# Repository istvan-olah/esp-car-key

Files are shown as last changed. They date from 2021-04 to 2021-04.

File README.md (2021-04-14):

## Automatic car unlock when nearby

 The main issue which this application solves is human forgetfulness, specifically if the car door 
 was locked or not. From my own experience, happens around 40% of the time, that I do not remember it.

 Basic idea is to have a BLE device (a phone, or a smartwatch/fitbit) and when that device is near the car,
the door will open, when it is not in range anymore, the doors will lock automatically.

## How it works?

 The application is configured to search for a specific MAC Address, since they are unique it is considered
secure but there also can be other security features introduced, for example that the device has to be paired
or by implementing a handshake. 

 The configuration part should be done over bluetooth, with a BL serial connection. With this feature, we
don't have to worry about changing our watch/phone, because the app only has to be reconfigured, 
 not reprogrammed.

## Pre-requisites

  - ESP 32-WROOM
  - A relay with 2 separate circuits
  - A remote car key motherboard
  - A BLE device (Android phone/Smartwatch/Fitbit)
  - 3 LED-s with 220 Ohm resistors
  - A 2-way switch
  - A buzzer
  - A DC-to-DC 5v-3.3v converter

## Schematics

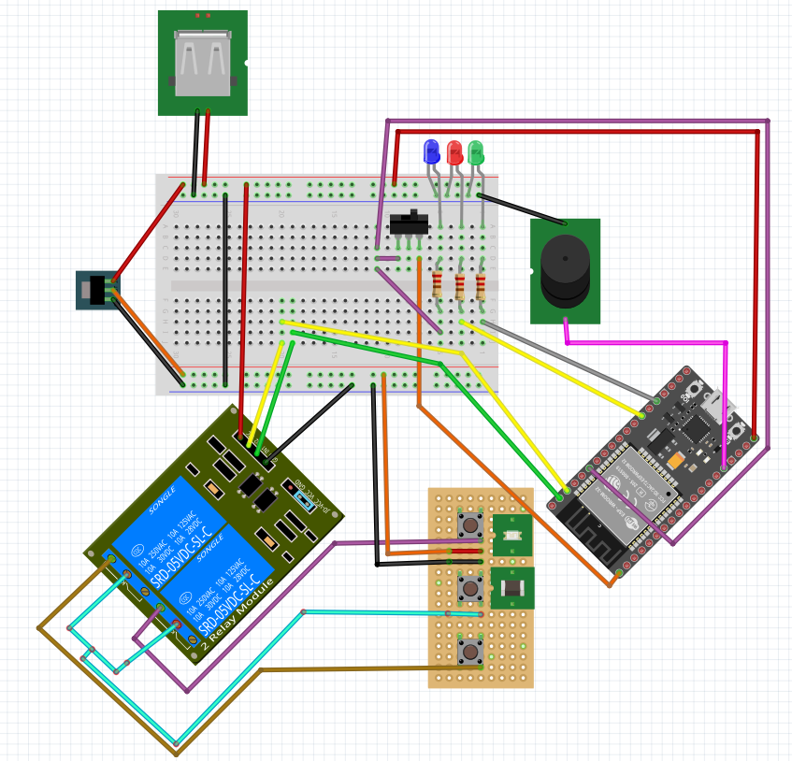
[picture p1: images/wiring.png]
Schematics


### Why use relays?

If we look closely, we can see that we have 2 circuits here. The one which contains the ESP-32
and the one which contains the key motherboard. For safety purposes I made it like this, so we won't
burn the key component, which is the most expensive part of the project and also the one which we have no
schematics or information about it whatsoever. 

## Wiring

### Power connections
 - 5v - ESP IN
 - GND - ESP GND
 - 5v - DC-DC converter input
 - GND - DC-DC converter GND
 - DC-DC output - Key input (where normally the battery goes)
 - GND - Key GND (where normally the battery goes)

### ESP Connections:
 - GPIO 13 - Buzzer
 - GPIO 2 - Green LED (turns on for 1 second when the car is unlocked)
 - GPIO 4 - Red LED (turns on for 1 second when the car is locked)
 - 3.3V - Switch input
 - GPIO 13 - Switch output
 - GPIO 22 - Switch output
 - GPIO 23 - Relay IN-1
 - GPIO 22 - Relay IN-2

 ### Relay connections:
 - COM1 & COM2 - Key common (it can be found with a multimeter, 
   all buttons on the key have that connection in common)
 - NO1 - Key close button's leg 
 - NO2 - Key open button's leg

## 3D Models

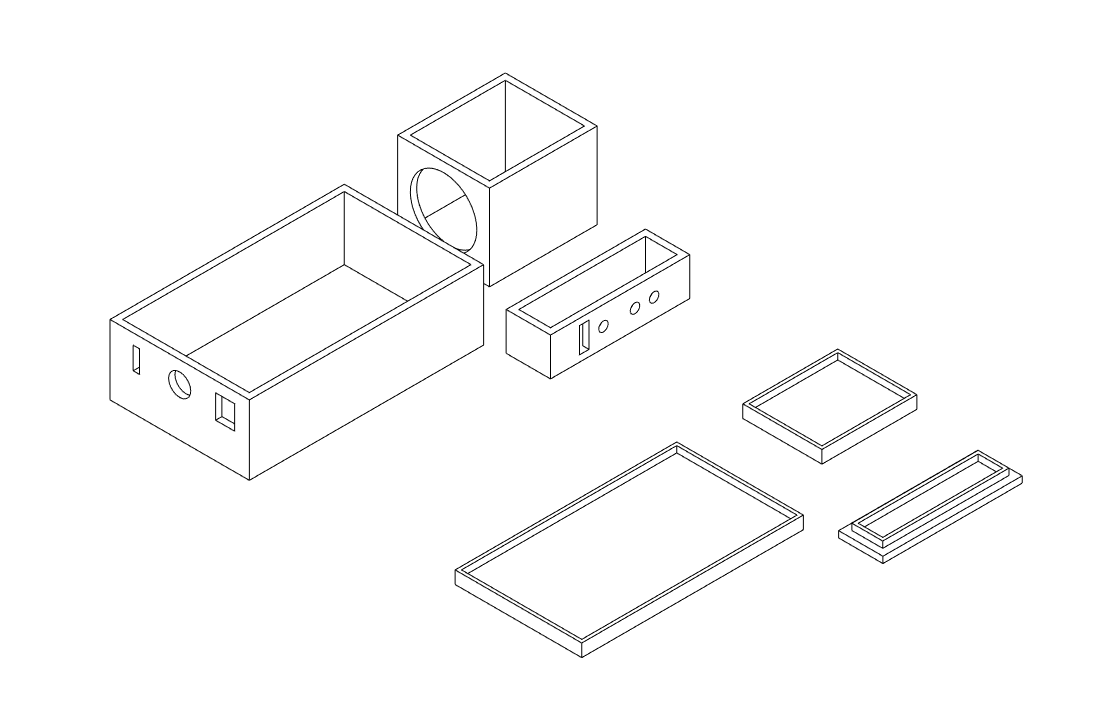
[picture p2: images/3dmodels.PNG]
3D Models


### Final status

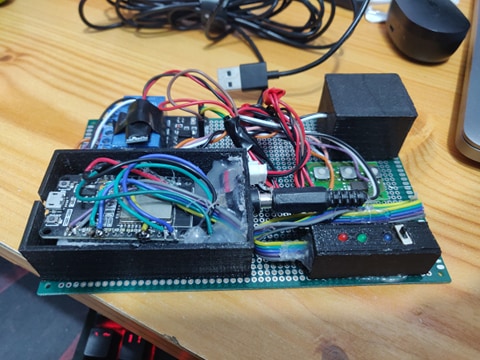
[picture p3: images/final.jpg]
Final


## Set up

 - Write the software onto the hardware using Arduino IDE
 - Download `Serial Bluetooth Terminal` from the [google play store](https://play.google.com/store/apps/details?id=de.kai_morich.serial_bluetooth_terminal&hl=en&gl=US)
 - Turn the switch on the ESP on and pair with the ESP (The name is set through the code)
- Send the following text to the device: 
  `|aa:bb:aa:bb:aa:bb;3500;5200;1100;4750;3;1000|`
     - The first is the mac address of the BLE device which is used as key
     - Second is the open delay (how much to wait after a scan whilst unlocked)
     - Third is the open timeout (how much to wait after the car was unlocked)
     - Fourth is the closed delay (how much to wait after a scan whilst locked)
     - Fifth is the closed timeout (how much to wait after the car was locked)
     - Sixth is the not found in a row (how many scans to wait to close the car if key not found)
     - Seventh is how much time to "press" the buttons on the key (different for each key)

## Putting it in the car 
  Please don't mind the fact that I haven't cleaned the interior in a while

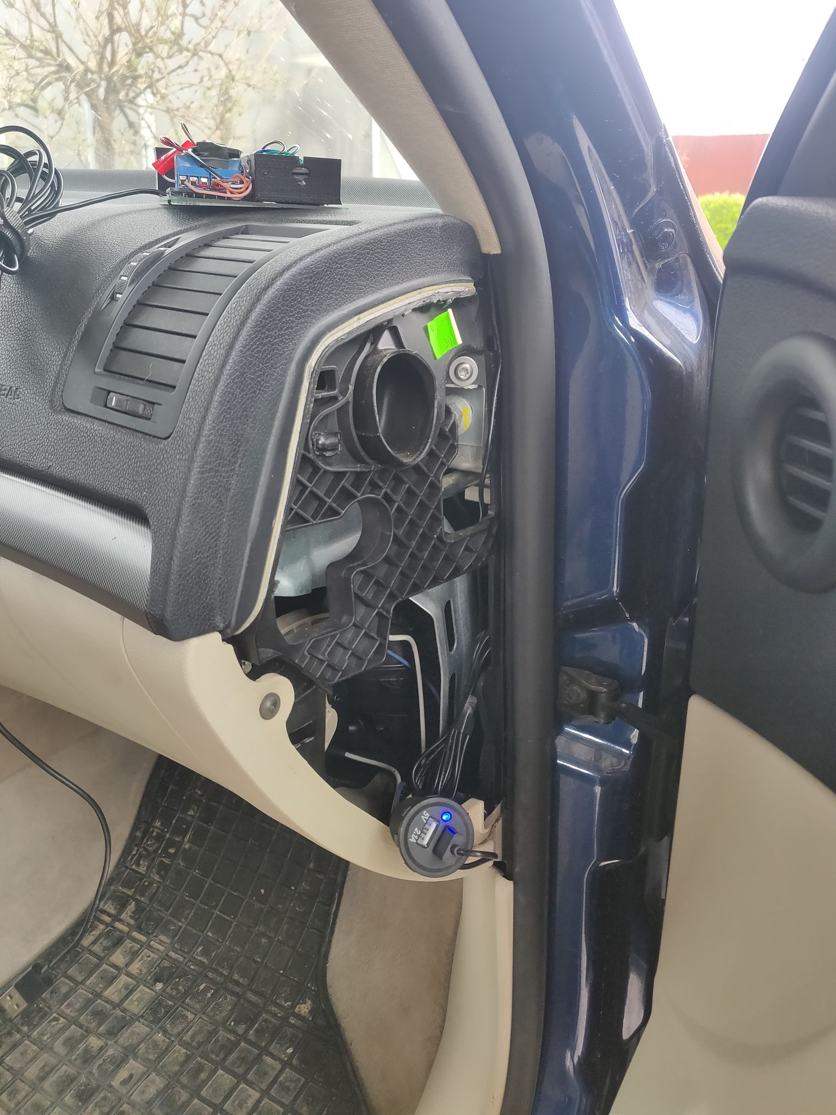
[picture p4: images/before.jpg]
Before
  
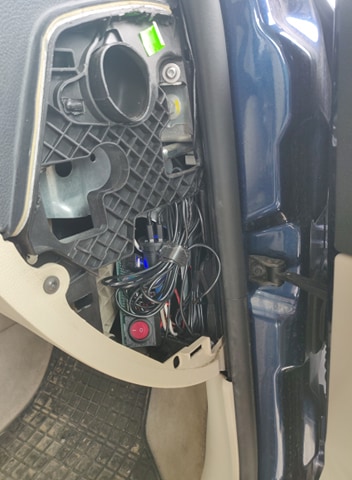
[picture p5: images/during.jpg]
During
  
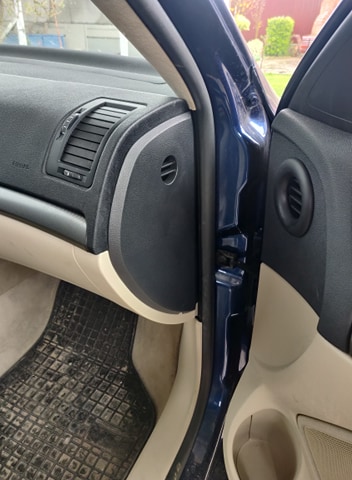
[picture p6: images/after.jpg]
After
  

## Demo

- [Open](https://drive.google.com/file/d/1vdPQ3_-kpQKyuDBrLKMNAIiMtcbKEesC/view?usp=sharing)
- [Close](https://drive.google.com/file/d/1vZy_R_4CrWvbVkuXrSSYAppPH0XH2bDy/view?usp=sharing)

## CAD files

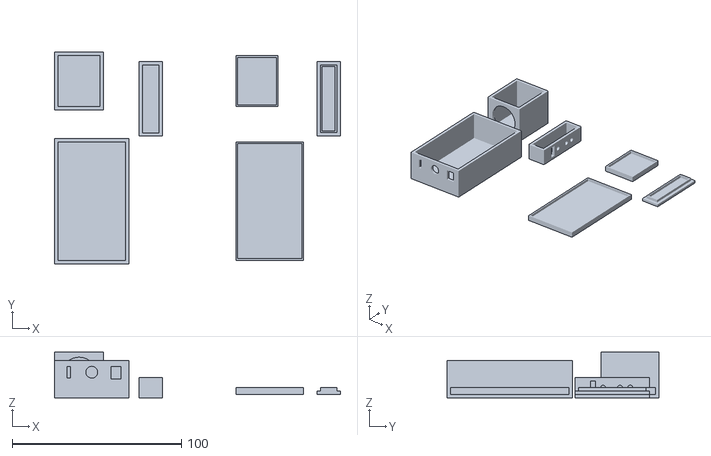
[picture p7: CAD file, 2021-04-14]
models/CarOpenerV2.stl
168.8 x 124.9 x 27.0

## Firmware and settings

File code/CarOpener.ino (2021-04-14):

#define OPEN_LED 2
#define CLOSE_LED 4
#define OPEN 22
#define CLOSE 23
#define BUZZER 13
#define SETUP_BUTTON 21

#include <Preferences.h>
Preferences prefs;

String getValue(String data, char separator, int index);
void configure();
void saveSettings();
void loadSettings();

struct Settings {
  String bleAddress;
  int openDelay;
  int openTimeout;
  int closedDelay;
  int closedTimeout;
  int notFoundInARow;
  int onDelay;
};

Settings* settings = NULL;

#include <BluetoothSerial.h>

BluetoothSerial* SerialBT;

#include <BLEDevice.h>

static BLERemoteCharacteristic* pRemoteCharacteristic;

BLEScan* pBLEScan;
BLEScanResults foundDevices;

static BLEAddress *Server_BLE_Address;
String Scaned_BLE_Address;
void checkRestart();
boolean paired = false;
boolean found = false;
class MyAdvertisedDeviceCallbacks: public BLEAdvertisedDeviceCallbacks 
{
    void onResult(BLEAdvertisedDevice advertisedDevice) {
      Server_BLE_Address = new BLEAddress(advertisedDevice.getAddress());
      Scaned_BLE_Address = Server_BLE_Address->toString().c_str();
      
      if (Scaned_BLE_Address == settings->bleAddress) {
        found=true;
      }
    }
};

void buzz() {
  digitalWrite(BUZZER, HIGH);
  delay(50);
  digitalWrite(BUZZER, LOW);
}

void setup() {
    loadSettings();

    pinMode(OPEN,OUTPUT);
    pinMode(CLOSE,OUTPUT);
    digitalWrite(OPEN, HIGH);
    digitalWrite(CLOSE, HIGH);
    pinMode(OPEN_LED,OUTPUT);
    pinMode(CLOSE_LED,OUTPUT);
    pinMode(BUZZER,OUTPUT);
    buzz();
    pinMode(SETUP_BUTTON,INPUT);
    if(digitalRead(SETUP_BUTTON) == HIGH) {
      configure();
      ESP.restart();
    }
    
    BLEDevice::init("");
    pBLEScan = BLEDevice::getScan(); //create new scan
    pBLEScan->setAdvertisedDeviceCallbacks(new MyAdvertisedDeviceCallbacks()); //Call the class that is defined above 
    pBLEScan->setActiveScan(true); //active scan uses more power, but get results faster

}

bool searchDevice() {
  found = false;
  pBLEScan->start(3); 
  return found;
}

void foundDevice() {
  paired = true;
  digitalWrite(OPEN_LED, HIGH);
  digitalWrite(OPEN, LOW);
  delay(settings->onDelay);
  digitalWrite(OPEN_LED, LOW);
  digitalWrite(OPEN, HIGH);
  buzz();
  delay(settings->openTimeout);
}

void deviceLost() {
  int retries = settings->notFoundInARow;
  while (retries > 0) {
    searchDevice();
    if (found) {
      return;  
    }
    retries--;
  }
  paired = false;
  digitalWrite(CLOSE_LED, HIGH);
  digitalWrite(CLOSE, LOW);
  delay(settings->onDelay);
  digitalWrite(CLOSE_LED, LOW);
  digitalWrite(CLOSE, HIGH);
  buzz();
  buzz();
}

void loop() {
  searchDevice();
  if(found && !paired) {
      foundDevice();
  }
  else if(!found && paired) {
      deviceLost();
  }
  if(paired){
    delay(settings->openDelay);
  } else {
    delay(settings->closedDelay);
  }
}

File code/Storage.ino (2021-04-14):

//**************************************************************************************************************************
// COMMON
//**************************************************************************************************************************
String getValue(String data, char separator, int index) {
  int found = 0;
  int strIndex[] = { 0, -1 };
  int maxIndex = data.length() - 1;

  for (int i = 0; i <= maxIndex && found <= index; i++) {
    if (data.charAt(i) == separator || i == maxIndex) {
      found++;
      strIndex[0] = strIndex[1] + 1;
      strIndex[1] = (i == maxIndex) ? i + 1 : i;
    }
  }
  return found > index ? data.substring(strIndex[0], strIndex[1]) : "";
}

//**************************************************************************************************************************
// PERSISTENT STORAGE
//**************************************************************************************************************************
void configure() {
  if (SerialBT == NULL) {
    SerialBT = new BluetoothSerial();
  }
  SerialBT->begin("Octavia");
  bool started = false;
  bool finished = false;

  String settingsString = "";
  char value;
  while (started == false) {
    value = SerialBT->read();
    if (value == '|') {
      started = true;
      while (finished == false) {
        if (SerialBT->available()) {
          char anotherOne = SerialBT->read();
          if (anotherOne == '|') {
            SerialBT->println("Ok");
            finished = true;
          } else {
            settingsString += anotherOne;
          }
        }
        delay(20);
        checkRestart();
      }
      checkRestart();
    }
    checkRestart();
    if (value == '*') {
      SerialBT->println(getSettings().c_str());
    }

  }
  settings->bleAddress = getValue(settingsString, ';', 0);
  settings->openDelay = getValue(settingsString, ';', 1).toInt();
  settings->openTimeout = getValue(settingsString, ';', 2).toInt();
  settings->closedDelay = getValue(settingsString, ';', 3).toInt();
  settings->closedTimeout = getValue(settingsString, ';', 4).toInt();
  settings->notFoundInARow = getValue(settingsString, ';', 5).toInt();
  settings->onDelay = getValue(settingsString, ';', 6).toInt();

  saveSettings();
  SerialBT->disconnect();
  SerialBT->end();
  delete SerialBT;
}

void checkRestart() {
  if (digitalRead(SETUP_BUTTON) == LOW) {
    delay(1000);
    if (digitalRead(SETUP_BUTTON) == LOW) {
      ESP.restart();
    }
  }
}

void saveSettings() {
  prefs.begin("car");
  prefs.putString("address", settings->bleAddress);
  prefs.putInt("openD", settings->openDelay);
  prefs.putInt("openT", settings->openTimeout);
  prefs.putInt("closedD", settings->closedDelay);
  prefs.putInt("closedT", settings->closedTimeout);
  prefs.putInt("notFound", settings->notFoundInARow);
  prefs.putInt("onDelay", settings->onDelay);
  prefs.end();
}

void loadSettings() {
  prefs.begin("car");
  settings = new Settings();
  settings->bleAddress = prefs.getString("address");
  if (settings->bleAddress == "") {
    settings->bleAddress = "aa:bb:aa:bb:aa:bb";
    settings->openDelay = 3000;
    settings->openTimeout = 5000;
    settings->closedDelay = 1000;
    settings->closedTimeout = 5000;
    settings->notFoundInARow = 3;
    settings->onDelay = 1000;
  }
  else {
    settings->bleAddress = prefs.getString("address");
    settings->openDelay = prefs.getInt("openD");
    settings->openTimeout = prefs.getInt("openT");
    settings->closedDelay = prefs.getInt("closedD");
    settings->closedTimeout = prefs.getInt("closedT");
    settings->notFoundInARow = prefs.getInt("notFound");
    settings->onDelay = prefs.getInt("onDelay");
  }
  prefs.end();
}

String getSettings() {
  String result = String();
  result += "Address: ";
  result += String(settings->bleAddress);
  result += "\nOpen delay: ";
  result += String(settings->openDelay);
  result += "\nOpen timeout: ";
  result += String(settings->openTimeout);
  result += "\nClosed delay: ";
  result += String(settings->closedDelay);
  result += "\nClosed timeout: ";
  result += String(settings->closedTimeout);
  result += "\nNot found in a row: ";
  result += String(settings->notFoundInARow);
  result += "\nOn delay: ";
  result += String(settings->onDelay);
  return result;
}
